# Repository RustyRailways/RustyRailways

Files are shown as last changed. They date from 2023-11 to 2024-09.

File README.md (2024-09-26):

# Rusty Railways

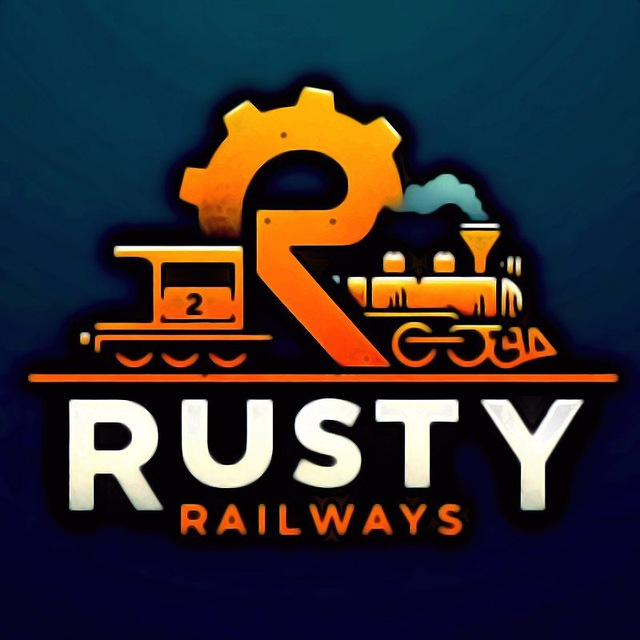
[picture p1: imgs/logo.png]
Rusty Railways Logo


## Description

Group Project by [**lucaSartore** (Sartore Luca)](https://github.com/lucaSartore), [**cattai-lorenzo** (Cattai Lorenzo)](https://github.com/cattai-lorenzo), [**MrLakige** (Callegari Michele)](https://github.com/MrLakige), [**Technorico** (Peruzzo Federico)](https://github.com/Technorico)
for [Embedded Software for The Internet of Things - 145996](https://unitn.coursecatalogue.cineca.it/insegnamenti/2023/95013/2019/10002/10712?annoOrdinamento=2019) taught by professor [Kasim Sinan Yildirim](https://webapps.unitn.it/du/it/Persona/PER0212812/Didattica) at [University of Trento, DISI Department](https://www.disi.unitn.it/).

This is a system that automates the motion of Lego trains and rail switches.
You can tell the system in which station you want a train to go (either using an HTTP request or using our GUI),
and the system will figure out the best way to achieve the goal, even moving trains that are on your
way if necessary. 

## Video

Watch the video (https://youtu.be/J4SjKY6N7vM)

## Components

The system is implemented using 5 different components:

 - `The Master`: This is the component that does all the calculations to find the optimal path, and then controls the trains and the switches, you can learn more about the master [here](./master/readme.md)
 - `The Client`: ([Godot](https://godotengine.org/) based client to create the train track and control/monitor the train system), you can learn more about the client [here](./client/README.md)
 - `The Map`: The map is a support data structure (a modified graph in particular) used by the master, you can learn more about the master [here](./map/readme.md)
 - `The Common Infrastructure`: The common infrastructure defines some basic messages that all components need to communicate with each other, as well as the IPs and the hardware abstraction layer traits, you can learn more about the master [here](./common_infrastructure/readme.md)
 - `The Trains`: You can learn more about the code that manages the trains [here](./train/rust/readme.md)
 - `The Switches`: You can learn more about the code that manages the switches [here](./switch/readme.md)

## Documentation

- [Common infrastructure documentation](https://rustyrailways.github.io/RustyRailways/common_infrastructure/doc/common_infrastructure/index.html)
- [Map documentation](https://rustyrailways.github.io/RustyRailways/map/doc/map/index.html)
- [Master documentation](https://rustyrailways.github.io/RustyRailways/master/doc/master/index.html)
- [Railway sim map documentation](https://rustyrailways.github.io/RustyRailways/railway_sim_map/doc/railway_sim_map/index.html)<br>
- [Switch documentation](https://rustyrailways.github.io/RustyRailways/switch/html/index.html)<br>
- [Train documentation](https://rustyrailways.github.io/RustyRailways/train/doc/locomotive/index.html)<br>

## Installation

Here you can find a quick list of the things you need to do, to try our project yourself.

### Master Installation
The current implementation of the master runs on a Linux system (e.g. Raspberry Pi with Raspberry Pi OS) so to run it, you just need to install the [regular rust toolchain](https://www.rust-lang.org/tools/install).
Given that we used a Hardware Abstraction Layer (HAL) to implement the master, with a bit more work, it can be executed on something smaller (like an ESP-32), if you are interested in this you can check out the train toolchain installation down below. 

### Train Toolchain Installation
The train code is written in embedded rust, with the [embedded-hal](https://github.com/rust-embedded/embedded-hal) and [embedded-svc](https://github.com/esp-rs/embedded-svc/tree/master) crates. To install the software needed to build for our target (The ESP-32) you can follow the tutorial [here](https://github.com/esp-rs/esp-idf-template?tab=readme-ov-file#prerequisites).

### Switch Toolchain Installation
To compile the switch code you can follow [this](./switch/readme.md) tutorial we have written.

### Client Installation
See [Client README.md](https://github.com/MrLakige/rusty_railways/blob/main/client/README.md).

### 3D Printing
Files to print the switch mechanism are located [here](./switch/hardware/Switch_3D_print/)
You can find a 3D printing tutorial [here](https://all3dp.com/1/cura-tutorial-software-slicer-cura-3d/).  

### Electronic Components

To build the switch PCB you can follow [this](switch#pcb) tutorial we have written

### Special Thanks

[FabLab UniTn](https://fablab.unitn.it/) for the space, tools and part of the materials used

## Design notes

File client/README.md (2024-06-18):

# Rusty Railways Client

This is a [Godot](https://godotengine.org/) based client to create the train track and control/see the status of the train system.

> [!WARNING]  
> This part of the project is currently broken, the code was fixed before the project presentation but never committed here properly with meaningful commits and comments in the code, I will try to do that whenever I find enough free time and willpower. Meanwhile you can use the [v0.1 release build](https://github.com/RustyRailways/RustyRailways/releases/tag/V0.1), it's an older version but it mostly works.

It lets you **Create** and **Edit** the **Train Track**, place the **NFC Tags**, **Trains** and **upload** (currently broken) everything to the Controller,
**Control** and **Monitor** the **Trains** and **Switches**.

### Screenshots
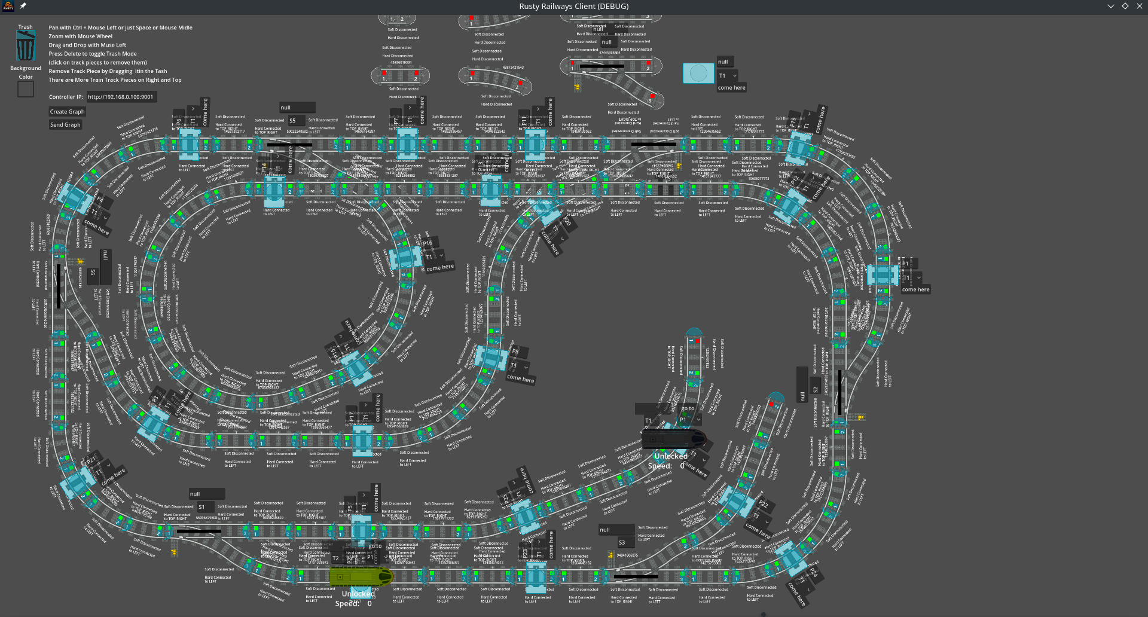
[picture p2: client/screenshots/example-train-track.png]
example-train-track


https://github.com/MrLakige/rusty_railways/assets/116217951/06c1ccc1-122a-48b4-8d96-e06f8fb9ee58

https://github.com/MrLakige/rusty_railways/assets/116217951/4c1d8071-14fc-486d-a815-6086c24b4450

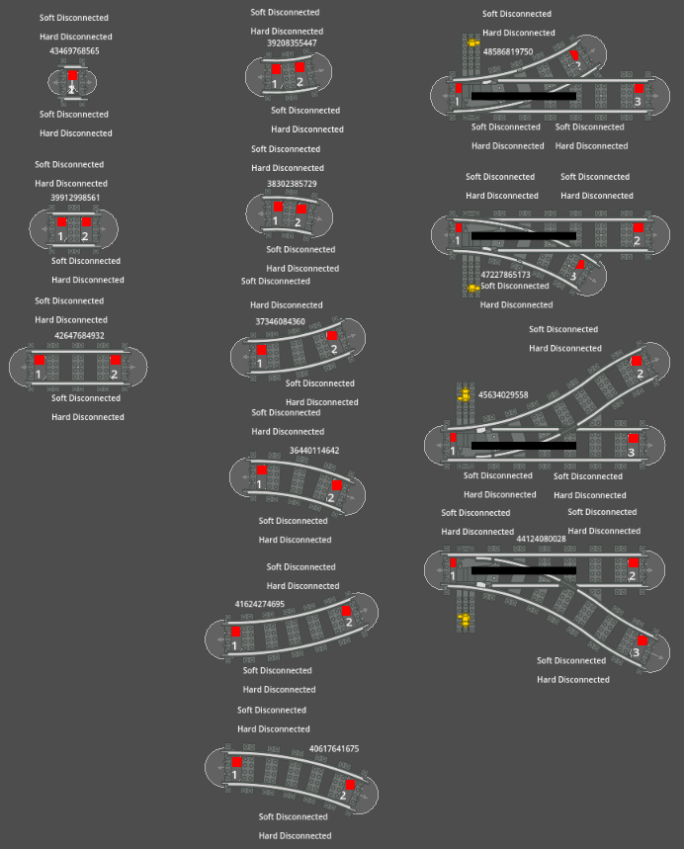
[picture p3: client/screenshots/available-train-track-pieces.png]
available-train-track-pieces


### Main Components
- Main (UI) ([Main.gd](./Main.gd) and [Main.tscn](./Main.tscn))
  - Create and Edit the Train Track, set IDs and Master IP

- HTTPIO ([HTTPIO.gd](./HTTPIO.gd))
  - Send move requests to Master (using HTTP with [this standard](./../master/src/high_level_controller#requests))

- Updaters ([TrainUpdatePosition.gd](./trains/TrainUpdatePosition.gd), [TrainUpdateStatus.gd](./trains/TrainUpdateStatus.gd), [TrainUpdateSpeed.gd](./trains/TrainUpdateSpeed.gd), [SwitchStateUpdater.gd](./trains/SwitchStateUpdater.gd))
  - Pools Train Positions, States, Speeds and Switch States data from Master (using HTTP with [this standard](./../master/src/high_level_controller#requests))

### Installation (from pre-made builds)
Download the latest master build for your OS from the [latest release page](https://github.com/MrLakige/rusty_railways/releases/latest) under `Assets` and launch it, the following builds are currently available:

- Linux x86_64
- Windows x86_64
- MacOS x86_64

https://github.com/MrLakige/rusty_railways/releases/download/V0.1/linux-x86_64-rusty-railways-client.x86_64

If you need a build for a different system and/or architecture please follow the [Installation (from source)](#Installation (from source)) section.

### Installation (from source)
Install the latest Godot 4 Version ([Steam App](https://store.steampowered.com/app/404790/Godot_Engine/), [Standalone Installer](https://godotengine.org/download/windows/), [Flatpak (Linux only)](https://flathub.org/apps/org.godotengine.Godot) or [WinGet (Windows only)](https://winstall.app/apps/GodotEngine.GodotEngine))

Clone the repository with 
```bash
git clone https://github.com/MrLakige/rusty_railways.git
```

Open 
```bash
./rusty_railways/client/project.godot
```

Go to `Project` -> `Export...` and choose one of the pre-made `Presets` or use `Add...` to add a new custom preset with a different system and/or architecture of your choice.

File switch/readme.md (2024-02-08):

# ESP-8266 Rail Track Switch Control System

This section of the repository contains the source code for an ESP-8266-based rail track switch control system. The code enables the `ESP-8266` to function as a web server, offering control over a servo-driven rail track switch. It is designed to set the correct path for trains.

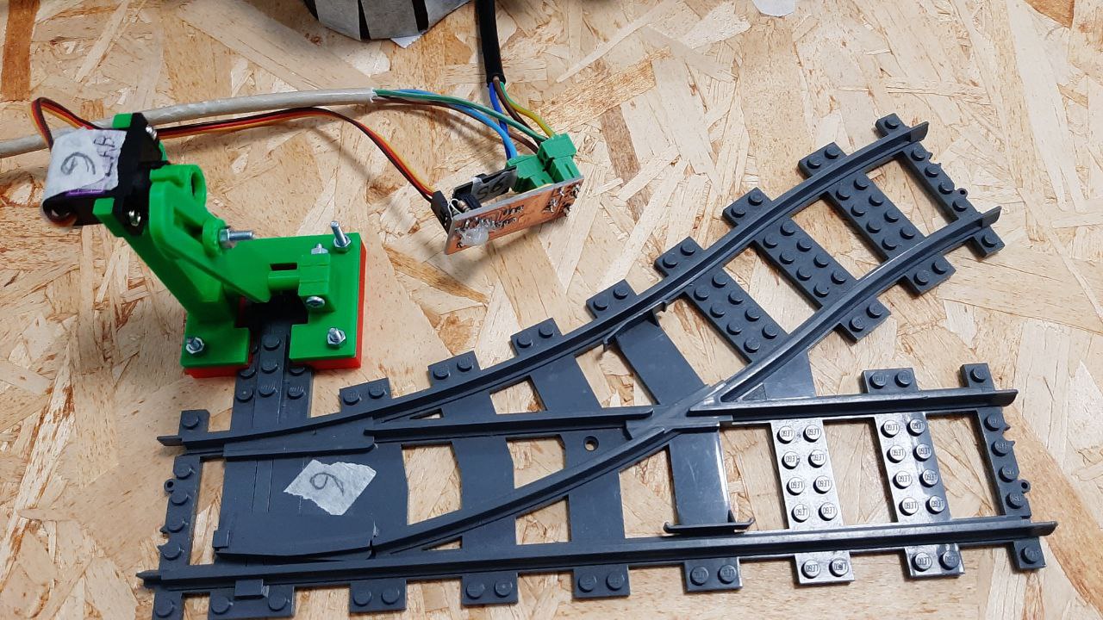
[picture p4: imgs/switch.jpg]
Switch Image


## Features
- The `ESP-8266` uses a REST API to interface with the other components of the project.
- Switch control commands can be transmitted via HTTP POST requests.

## Hardware
- The system utilizes a Servo motor (specifically, the `MSG90S`) to control the position of the rail track switch.
- WiFi connectivity is established using the built-in wireless functionality of the `ESP-8266` module.

## Code Overview
- The code includes essential libraries such as `ESP8266WiFi`, `WiFiClient`, `ESP8266WebServer`, `Arduino`, `Servo`, and `ArduinoJson`.
- Switch positions are defined based on user-configurable constants.
- The web server responds to HTTP GET requests with information about the switch and handles HTTP POST requests to control the switch position.

## Requirements
- [PlatformIO](https://platformio.org/platformio-ide) (Follow the [guide to download and configure](https://docs.platformio.org/en/latest/core/installation/index.html))
- PlatformIO compiler toolchain (Download [here](https://registry.platformio.org/platforms/platformio/espressif8266/installation))

## Configuration
1. Modify the WiFi credentials by adjusting the `STASSID` and `STAPSK` constants.
2. Specify the switch characteristics by defining the switch name and position angles for the servo in the code.
   (In our demo it is possible to select one of the predefined configurations of the six switches present on the map, using a compiler directive modifiable in the [platformio.ini](./platformio.ini))

## Usage
1. Connect the `ESP-8266` to the rail track switch control mechanism.
2. Flash the firmware using this command:  
   ```bash
      platformio run --target upload`
   ```
### Troubleshooting
#### If a library is not found
1. Run:  
    ```bash
    pio lib install
    pio update
    ```
#### If PlatformIO is not found
1. Ensure that PlatformIO and the toolchain are installed correctly.
2. Verify that the PlatformIO global variable is set.  
   Command:
   ```bash
      source /your_local_path_to/ENV/bin/activate
   ```
## Supported Hardware Parts:
>[!CAUTION]
>⚠️ **BASIC CNC AND ELECTRONICS KNOWLEDGE IS NEEDED TO REPRODUCE BELOW STEPS** ⚠️
### PCB
Files to create the PCBs are located [here](./hardware/Switch_PCB).
#### To Design and Mill a PCB:
You will require the following software:
- [KiCad](https://www.kicad.org/)
- [FlatCAM](http://flatcam.org/)
- GRBL Controller, like [Candle](https://github.com/Denvi/Candle)

#### To mill the PCB of the Switch:
>[!IMPORTANT]
>GRBL Controller or a GCode for CNC/NC controller for your CNC is required.
1. Download the .nc files from [here](./hardware/Switch_PCB/FlatCAM/OutputFiles)
2. Load in the _CNC Program_ / _NC Code Feeder_ the [file](./hardware/Switch_PCB/FlatCAM/OutputFiles/Switch_PCB_ESP01-F_Cu.gbr_cnc_file.nc) with _F_Cu_ in his name, to make the isolation of the traces of the PCB circuit.
3. Then load in this sequence, the following files: [0.8mm](./hardware/Switch_PCB/FlatCAM/OutputFiles/Switch_PCB_ESP01-PTH_0.8mm.drl_cnc.nc), [1.0mm](./hardware/Switch_PCB/FlatCAM/OutputFiles/Switch_PCB_ESP01-PTH_1.0mm.drl_cnc.nc), [Edge_Cuts](./hardware/Switch_PCB/FlatCAM/OutputFiles/Switch_PCB_ESP01-Edge_Cuts.gbr_cutout_cnc.nc).

___
### Images for reference

<p float="left">
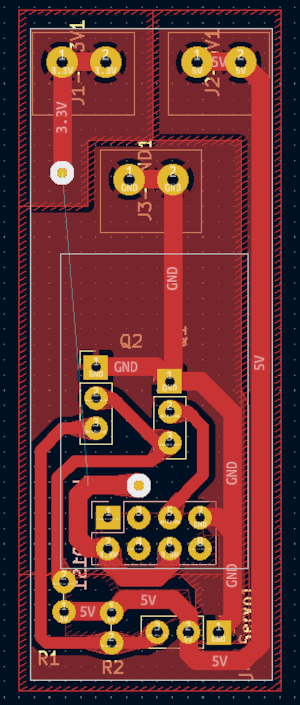
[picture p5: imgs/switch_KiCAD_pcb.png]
   
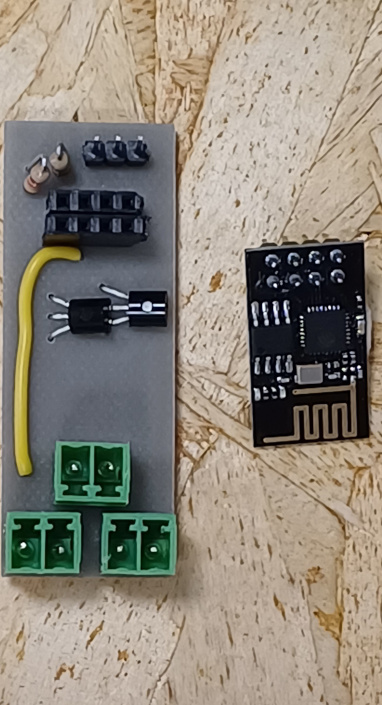
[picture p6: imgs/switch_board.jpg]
   
</p>

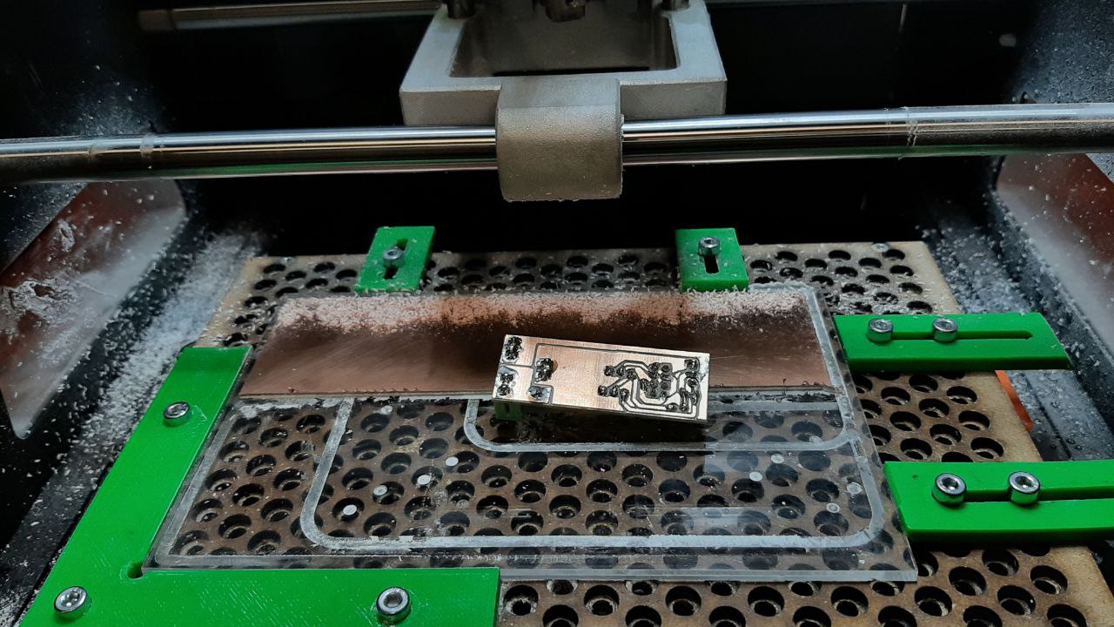
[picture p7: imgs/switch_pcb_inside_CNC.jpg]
Switch PCB inside CNC


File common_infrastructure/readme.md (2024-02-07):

# Common infrastructure

This crate defines some common components that are in use in all the other creates, in particular:

 - `Position` is an enum that represents all of the possible positions the train can be on, in reality, the position is identified by an RFID tag that can be read from an NFC reader, so the enum can be created from an array of 4 bytes.

 - `Train` is an enum that represents all the trains
 - `Switch` is an enum that represents all the switches in the map
- `urls` is a module that defines all the IPs and URLs of the components involved in the system
- `hals` is a module that defines some traits for the components involved in the system, these traits are used to abstract the hardware, to make it possible to run the same code on different hardware configurations. There are 3 main _HAL_s defined:
  - `GenericHal` is the _HAL_ that defines the basic functionalities, and all of the other HALs inherit from this.
  - `MasterHal` is the _HAL_ for the master/brain of the operation
  - `TrainHal` is the _HAL_ for the train
  - `HeartBeatManagerHal` is a _HAL_ for an optional component that can be used for additional safety that allows the system to detect if a component is disconnected. This is not in use in the current implementation of the master and the train
  
Note: the switch does not have a _HAL_ because our switches run on `ESP-8266` that are not supported in embedded rust.

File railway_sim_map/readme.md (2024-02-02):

# Railway sim map

This create contains a simulated version of the real world map, this is done by implementing the master's HAL and executing all the actions in a virtual world.

This has been used to develop the master quicker without having to debug on real world components

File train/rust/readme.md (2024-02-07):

# Locomotive Part

## Description

This section of the repository focuses on the train component of the project. Each train is equipped with an `ESP-WROOM-32` for motor control and communication via WiFi, along with an NFC RFID reader. The code is written in Rust, based on the Rust Embedded HAL framework. The benefits of using Rust Embedded include a common infrastructure used among all projects, better code reusability, and better memory safety.

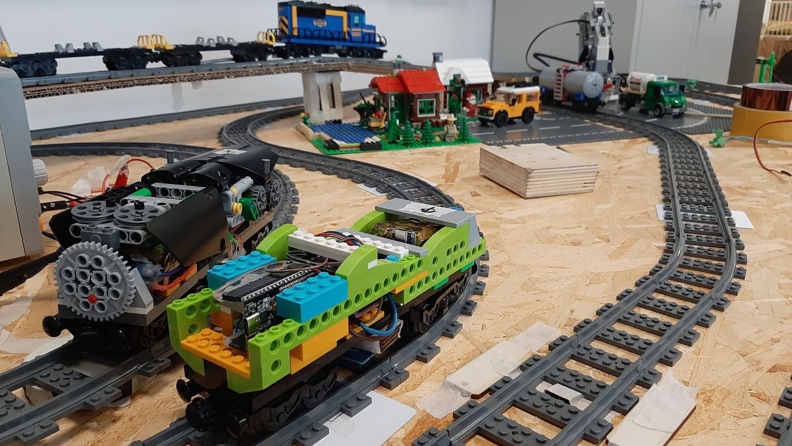
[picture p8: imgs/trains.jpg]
Trains Image


## Hardware schematics

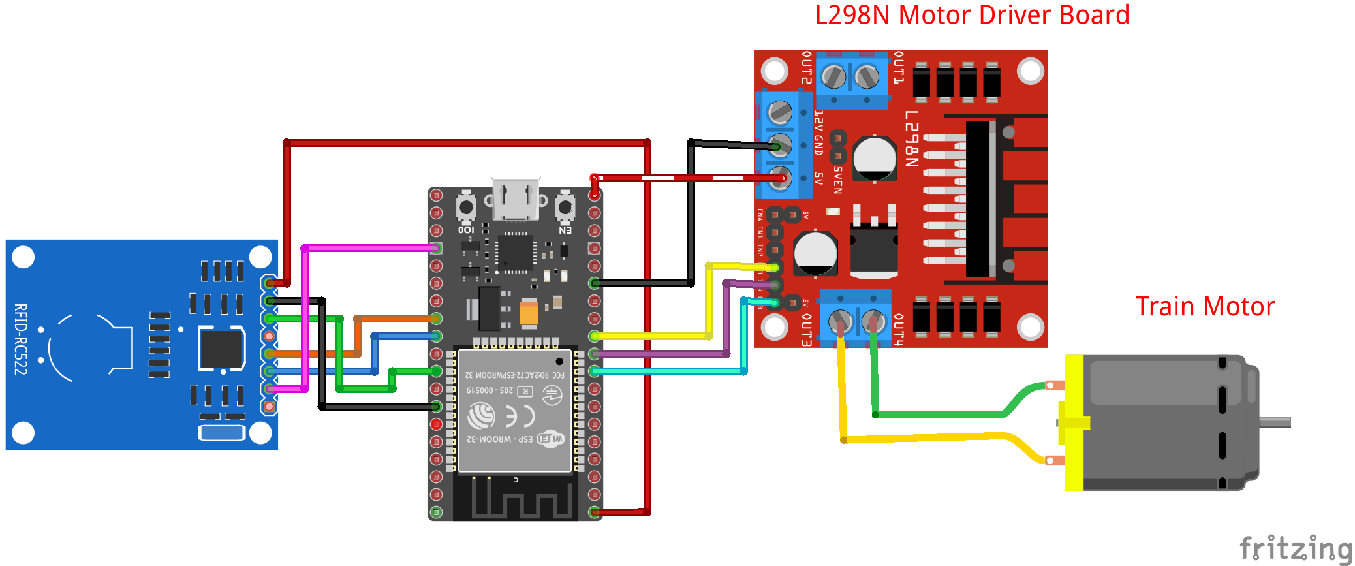
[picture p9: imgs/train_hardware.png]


 - Motor control pins:
    - pwm_pin      -> `GPIO25`
    - forward_pin  -> `GPIO26`
    - backward_pin -> `GPIO27`
 - NFC reader pins:
    - SCK          -> `GPIO15`
    - MISO         -> `GPIO16`
    - MOSI         -> `GPIO17`
    - SS/Reset     -> `GPIO18`

## Features

The features include reading NFC tags placed on the track, WiFi communication, and motor control. Each feature is implemented in specific files according to the Rust HAL framework.

## Hardware

Trains locomotives are composed of an `ESP-WROOM-32`, `H-bridge L298N`, `NFC/RFID reader MFRC-522`, and a `Li-Ion custom battery pack`.

## Requirements

Before proceeding, ensure that the main requirements are installed. Refer to the [main project guide](../../README.md) for details. Follow [this guide](https://github.com/esp-rs/esp-idf-template/tree/master#prerequisites) to download and install all the necessary files and toolchains required to run this part of the project.

### If Some Libraries Are Missing:

1. Run the following command to install the required dependencies:
    ```bash
    sudo apt-get install git wget flex bison gperf python3 python3-pip python3-venv cmake ninja-build ccache libffi-dev libssl-dev dfu-util libusb-1.0-0
    ```

2. If facing issues installing **libuv-dev**, follow this [solution](https://stackoverflow.com/questions/32438367/install-libuv-on-ubuntu-12-04):
    ```bash
    sudo apt-get install libudev-sys
    sudo apt-get install libudev-dev 
    ```

## Compile and Execution

1. Initialize:
   ```bash
   make init
   ```
3. Compile:
   ```bash
   make build
   ```
5. Connect the ESP32 and flash:
   ```bash
   make flash
   ```
7. (Optional) For debugging, check the serial output:
   ```bash
   make monitor
   ```

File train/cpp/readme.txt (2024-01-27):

command:
source ./ENV/bin/activate
platformio init --board esp12e

git clone https://github.com/Links2004/arduinoWebSockets.git

platformio run --target upload
pio device monitor

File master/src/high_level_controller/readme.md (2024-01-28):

# High level controller

The high level controller is the component that communicate with the GUI and control the
path finder and scheduler.

## Requests

The high level controller spawn a web server that can receive requests from the GUI.  
All the requests will be done at at the ip `IP_MASTER` and port `MASTER_PORT_VISUALIZER` (see the [common infrastructure](../../../common_infrastructure/src/urls.rs)).

The handler supported are:

 - `POST /add_request`: add a new request to the scheduler  
   examples:
    - `{"MoveTrain": ["T1","P3"]}`
    - `{"LockTrain": ["T1"]}`
    - `{"UnlockTrain": ["T1"]}`
 - `GET /train_position/{id}` return the position of the train  
   example: 
   - `"P1"`
 - `GET /train_status/{id}` return the status of the train,  
    examples: 
   - `"Locked"`
   - `"Unlocked"`
   - `"Moving"`
 - `GET /train_speed/{id}` return the speed of the train, as a signed 8-bit integer  
    example: 
   - `10`
 - `GET /switch_position/{id}` return the position of the switch  
    examples: 
   - `"Straight"`
   - `"Diverted"`

Note 1: `id` is an integer, and is the id of the train or switch.
for example `id=1` is equal to the train `T1` or the switch `S1`.

Note 2: All the get methods can return null if the train or switch is not found. 

## Response
 All the response are in TEXT format, if an error occurs the code will be `500` and the body will be the error message.

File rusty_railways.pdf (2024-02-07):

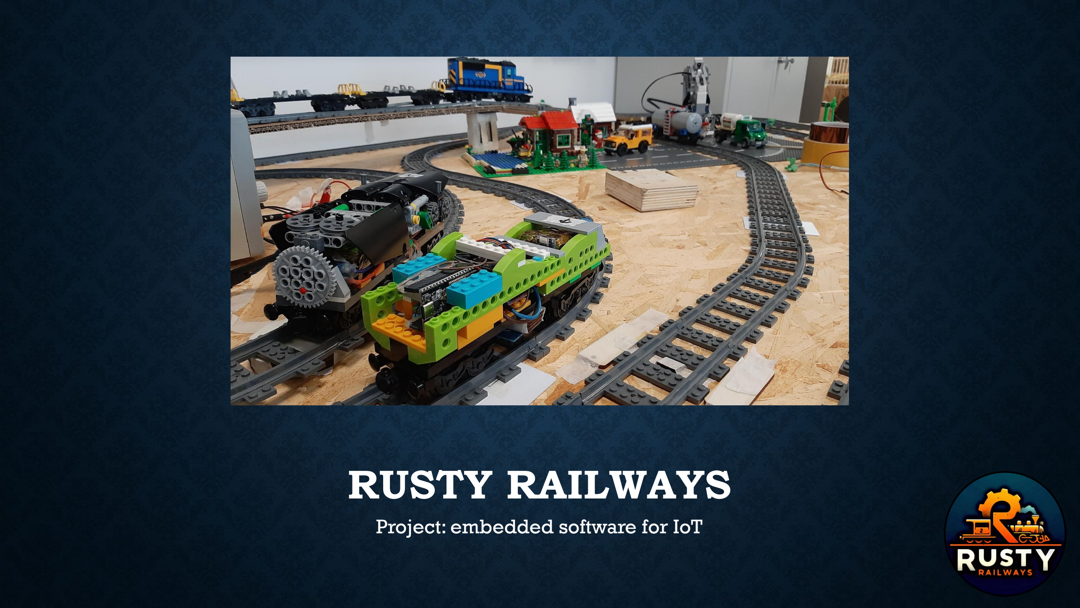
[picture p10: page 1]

# RUSTY RAILWAYS

## Project: embedded software for IoT

# MASTER

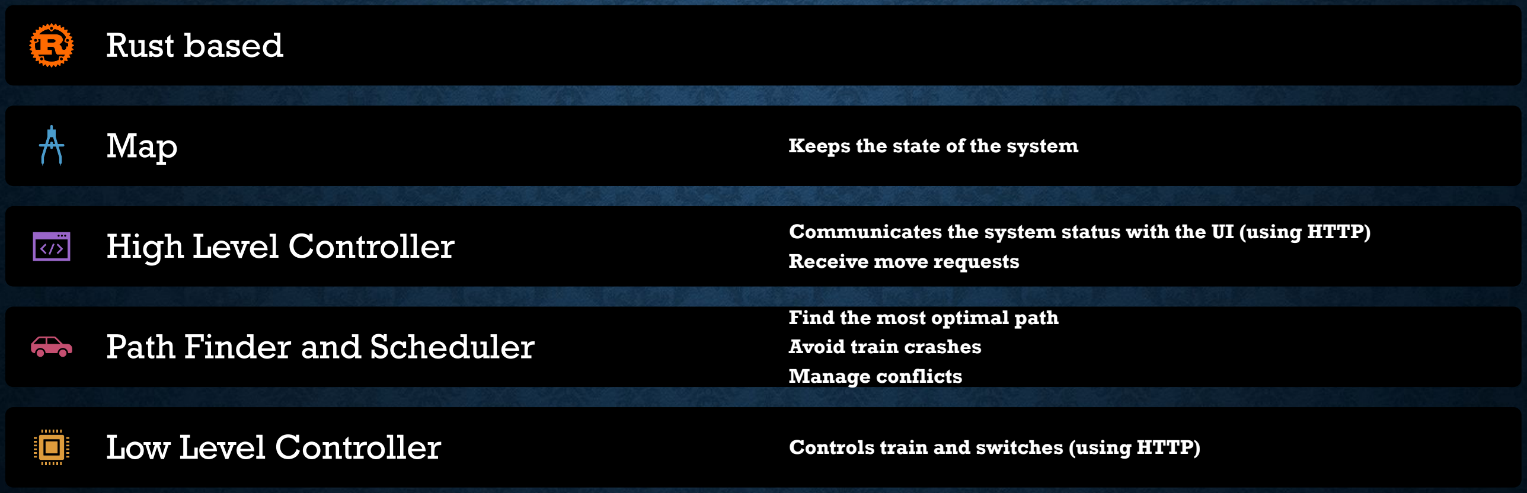
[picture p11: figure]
Rust based; Map; Keeps the state of the system; Receive move requests; Path Finder and Scheduler; Find the most optimal path; Avoid train crashes; Manage conflicts

High Level Controller | Communicates the system status with the UI (using HTTP)
Low Level Controller | Controls train and switches (using HTTP)

# TRAIN

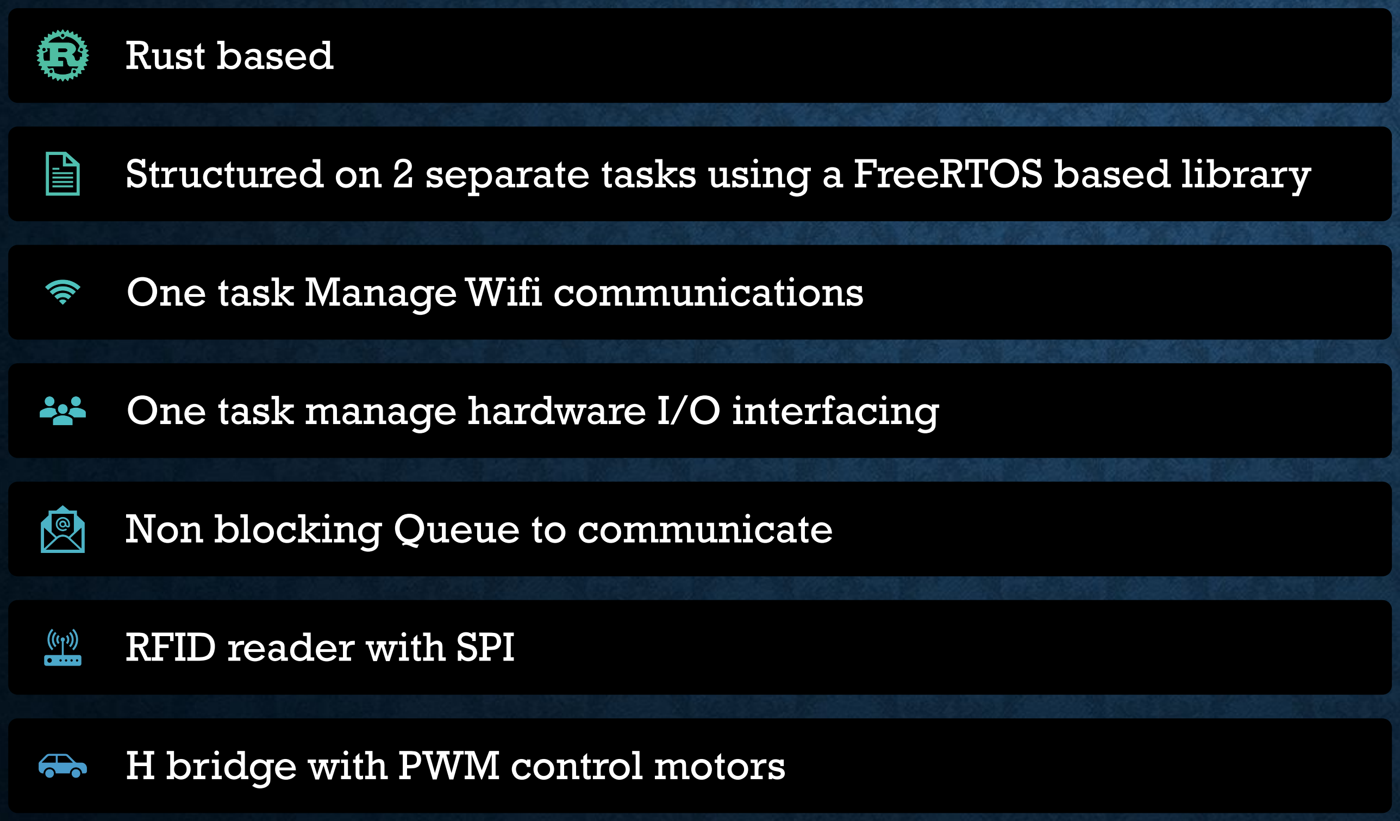
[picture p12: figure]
Rust based; One task Manage Wifi communications; Non blocking Queue to communicate; RFID reader with SPI; H bridge with PWM control motors
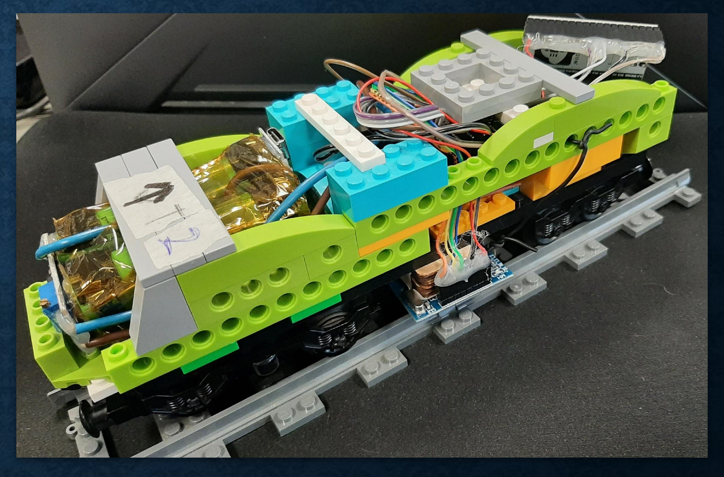
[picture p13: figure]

Structured on 2 separate tasks using a FreeRTOS based library

One task manage hardware I/O interfacing

# RAILWAY SWITCHES

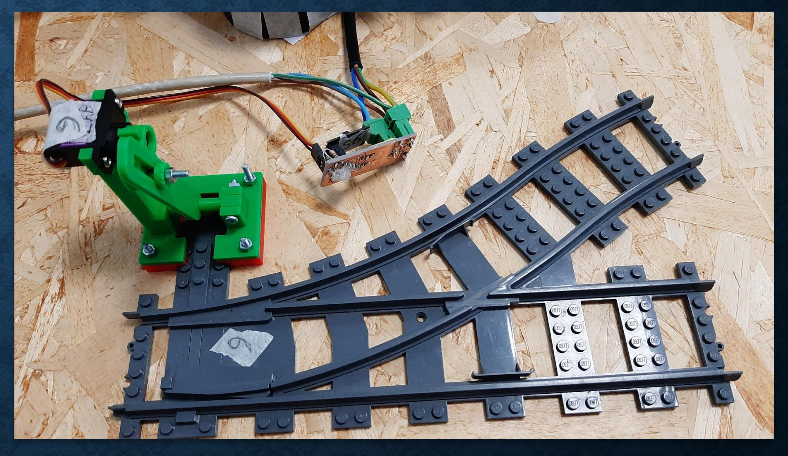
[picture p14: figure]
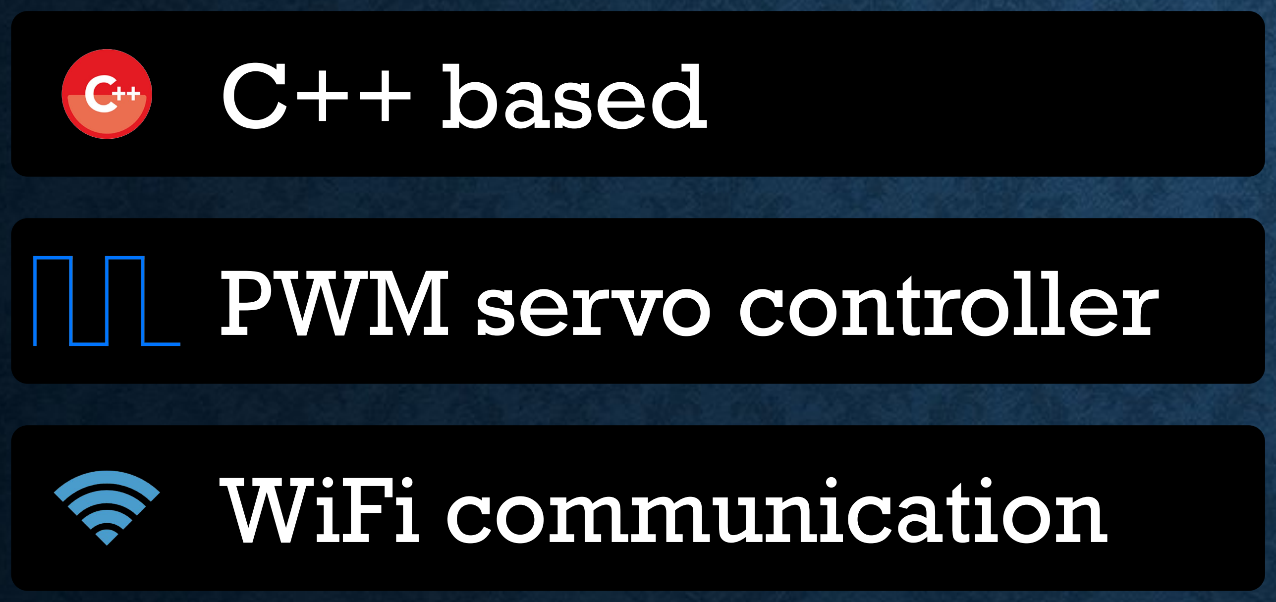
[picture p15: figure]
C++ based; PWM servo controller; WiFi communication

# CLIENT (GUI)

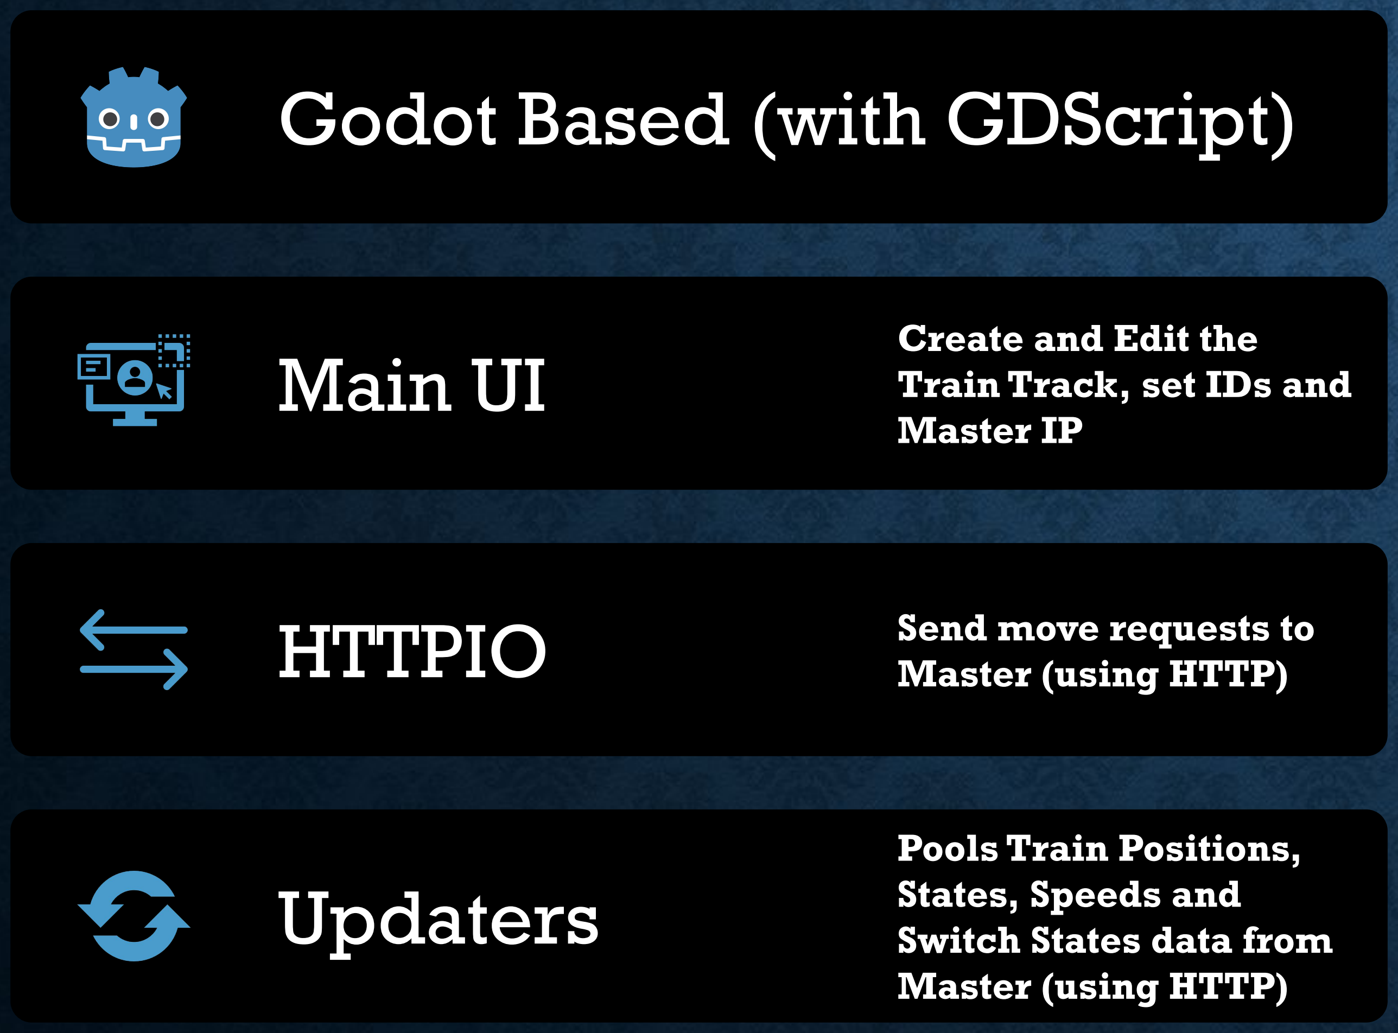
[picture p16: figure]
Godot Based (with GDScript); Main UI; Create and Edit the Train Track, set IDs and Master IP; HTTPIO; Send move requests to; Master (using HTTP); Updaters; Pools Train Positions, States, Speeds and Switch States data from Master (using HTTP)
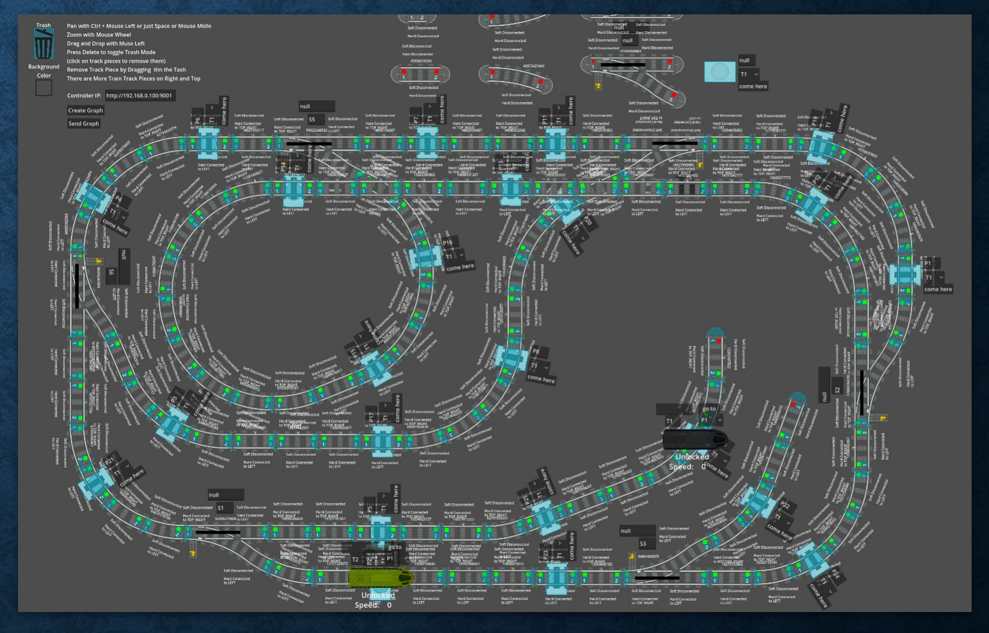
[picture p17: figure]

# STRUCTURE AND TESTING

## - All Rust components are split into hardware

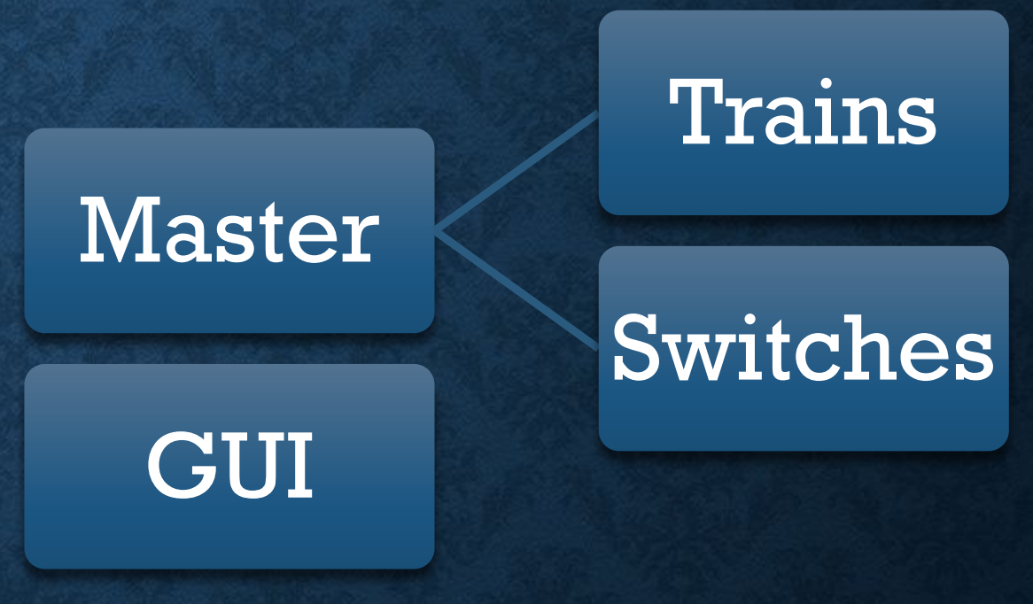
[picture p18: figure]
Master; Trains; Switches; GUI

## dependent and hardware independent parts

using rust’s Trait System Example (https://mrlakige.github.io/rusty_railways/common_infrastructure/doc/common_infrastructure/hals/trait.TrainHal.html)

## - The entire system has been recreated in a

simulation (https://github.com/MrLakige/rusty_railways/tree/main/railway_sim_map) to test all the master’s feature

## without the needs of a physical system

- The master has also 30+ automated unit | test (https://github.com/MrLakige/rusty_railways/blob/main/map/src/map_tests.rs#L115)
- All the code is fully covered by | documentation (https://mrlakige.github.io/rusty_railways/)

## tanks to doxygen and rustdoc

# FUTURE IMPLEMENTATIONS

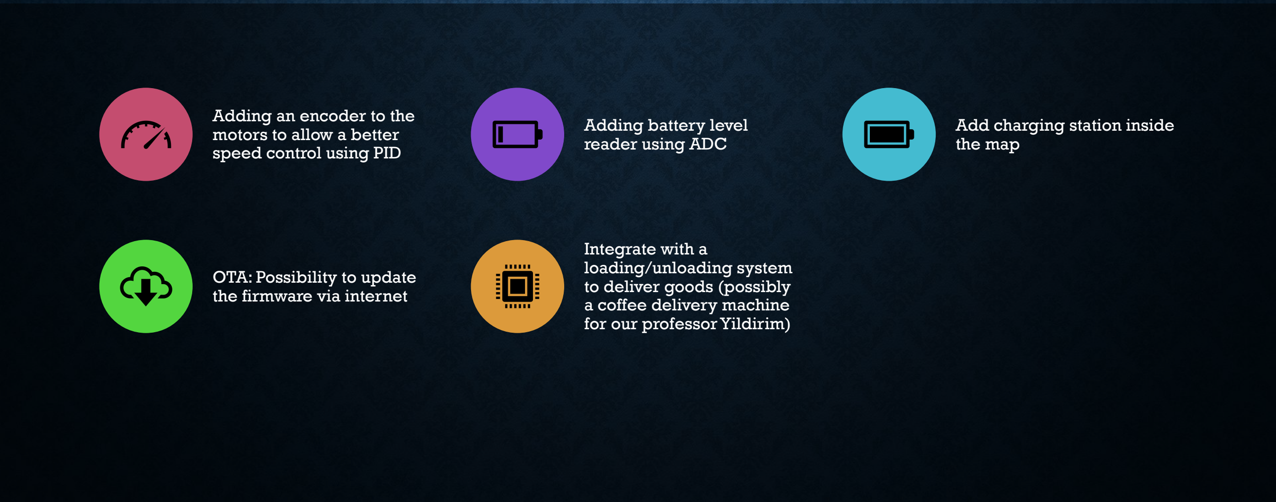
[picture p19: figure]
Adding an encoder to the motors to allow a better speed control using PID; Adding battery level reader using ADC; Add charging station inside the map; OTA: Possibility to update the firmware via internet; Integrate with a loading/unloading system to deliver goods (possibly a coffee delivery machine for our professor Yildirim)

# CONTRIBUTIONS

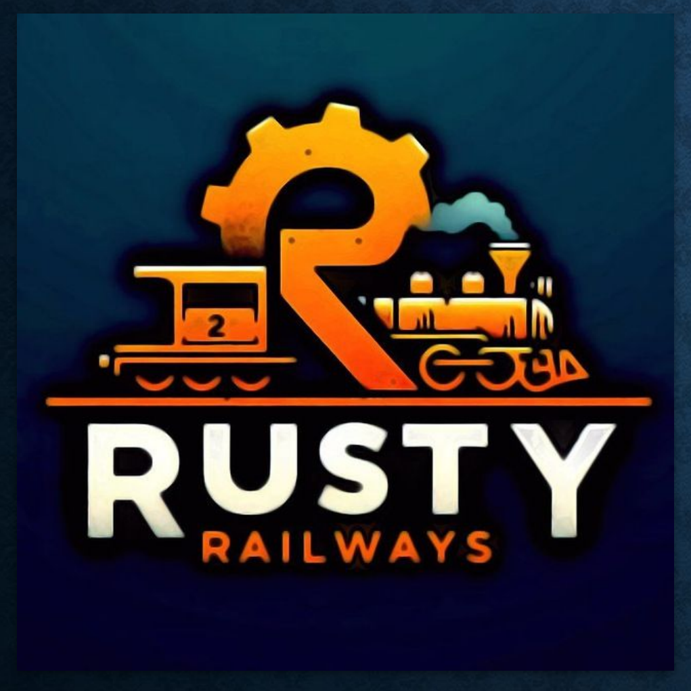
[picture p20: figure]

Master:

- Low Level Controller: Federico Peruzzo
- Path Finder And scheduler: Luca Sartore
- High Level Controller: Lorenzo Cattai

Trains: Luca Sartore and Michele Callegari

Switches: Michele Callegari

Graphical user interface: Lorenzo Cattai

Electronic Design, testing and manufacturing: Federico Peruzzo

3D Design: Luca Sartore

Git Repository: https://github.com/MrLakige/rusty_railways

A Special tanks to the UniTn FabLab Team!

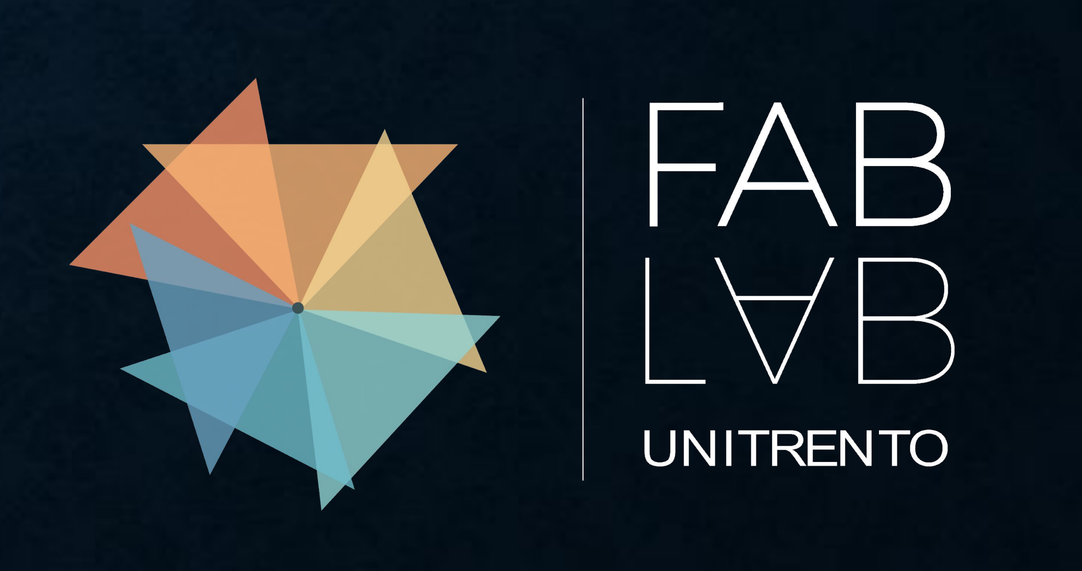
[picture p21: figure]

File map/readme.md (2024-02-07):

# Map

Basically, the map is a wrapper structure for a graph with some specific features that are used for our implementation.

In the graph, a node represents a position, (aka an NFC tag) in the real world.

The tags are used for:
 - Tel the train when to stop for a station
 - Track the position of the train and stop if it takes the wrong path
 - Regulate the train speed for tracks with different slope/curvature radius

A link in a map contains the length of the link and the maximum speed the train is allowed to reach on that track. The speed can be different depending on the direction the train is going (this is useful for example in a slope).

## Implementation

### The Initialized-Uninitialized States

The map is written using a generic-structure, where the generic parameters _S_ represent the states (that can be `Initialized` or `Uninitialized`).
Inside the graph, some `References` are used to point to `Nodes`, `Trains`, and `Switches`.
In the map, a reference is a structure that points to an object (e.g. a train has inside a reference to the station it is currently on).
The [references](references/mod.rs) can also have two states (`Initialized` or `Uninitialized`).  
To understand this distinction let's make an example with a reference to the position `P1`  

In the case of an Uninitialized map, a reference will just contain an enum
`Position::P1`. This is good for simplicity, as it avoids having to deal with pointers, it also allows us to make the map structure serializable and deserializable to JSON using `serde` and `serde/json`.
The only problem is that the performances are not as good compared with 
having a pointer/reference.

In the case of an Initialized map, the reference is replaced with a raw pointer, that allows for quick access to the item referenced.

#### The use of unsafe

We wanted to derive the serialize/deserialize trait, and this can only be done with the uninitialized state of the map, as we cannot deserialize a reference/pointer to a variable.  

Unfortunately as of today (02/2024), due to Rust characteristics and implementation, is impossible to decide to derive the serialize/deserialize (or any other Trait) only for a version with type _T_ of a generic structure (e.g. talking about our project we cannot derive _serialize_/_deserialize_ for Map\<_Uninitialized_> without also deriving it for Map\<_Initialized_>). To avoid this we have implemented manually the serialize/deserialize for the initialized reference, with just a panic that explains that the function should never be used.
Then we had to use raw pointers instead of references inside the initialized Map reference because using a lifetime would prevent us from implementing the deserialize trait.

## Map views

The map has many functionalities, to simplify the life of the user some `Views` have been created, in particular:
 - [Map creation view:](src/views/map_creation_view.rs) is a view used to quickly and easily build a map
 - [Map controller view:](src/views/map_controller_view.rs) is a view designed to control the map (e.g. move the train/the switches...)
 - [Map visualization view:](src/views/map_visualization_view.rs) is a view designed to give information about the map, like having the speed and status of trains
 - [Map navigation view:](src/views/map_visualization_view.rs) exposes some high-level APIs to navigate the map as a graph and find the best path
 - [Map factory:](src/views/map_factory.rs) is a factory that allow to create different views.

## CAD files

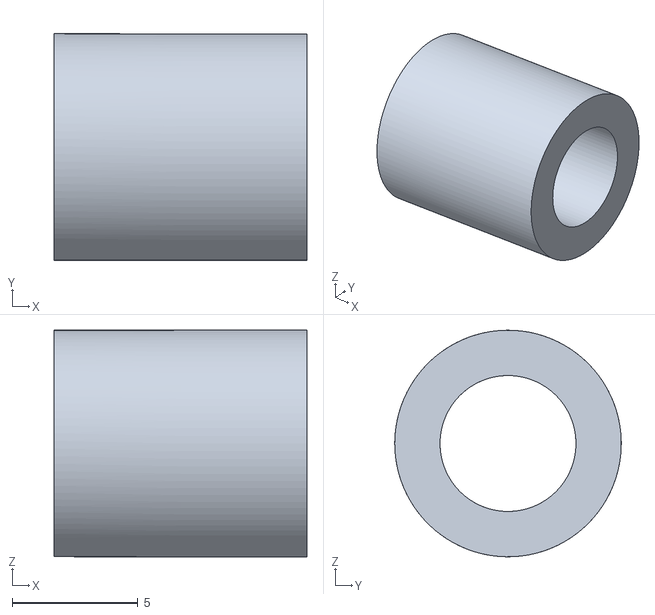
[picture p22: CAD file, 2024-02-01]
switch/hardware/Switch_3D_print/Spacer.stl
10.1 x 9.00 x 9.00

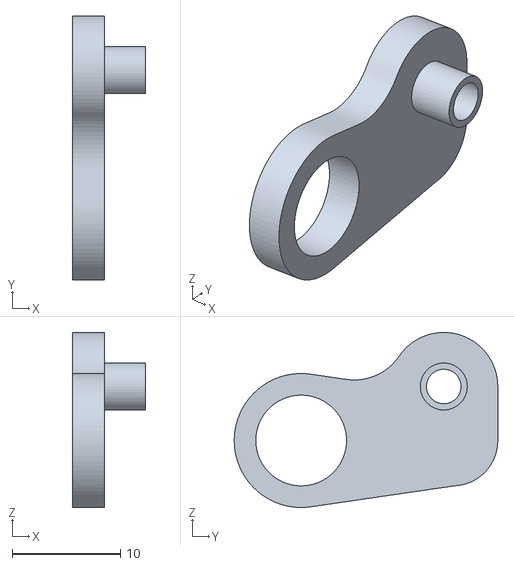
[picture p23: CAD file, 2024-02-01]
switch/hardware/Switch_3D_print/servo arm 2.stl
6.80 x 24.4 x 16.2

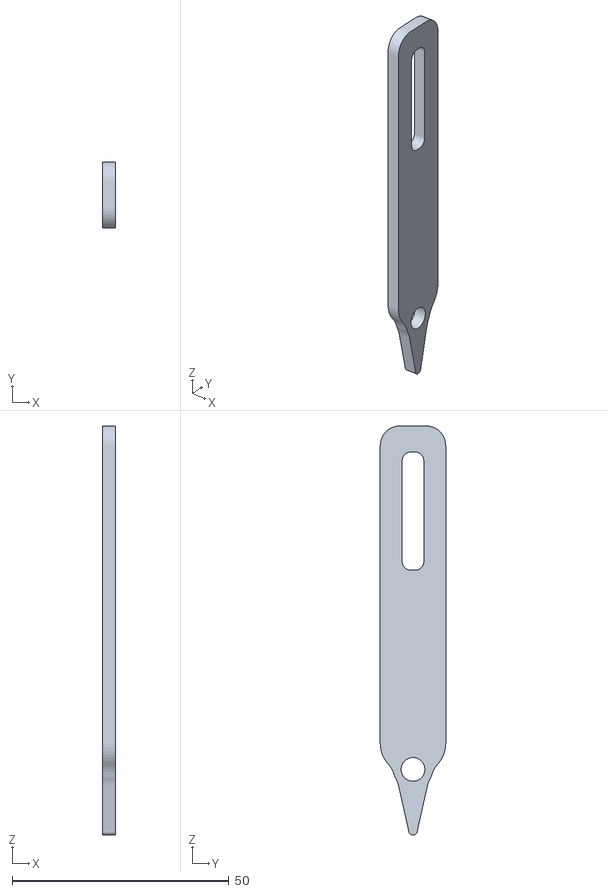
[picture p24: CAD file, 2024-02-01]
switch/hardware/Switch_3D_print/Perno.stl
3.10 x 15.1 x 94.4

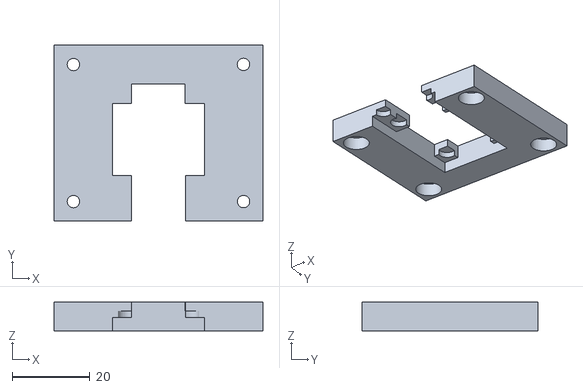
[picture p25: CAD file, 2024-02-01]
switch/hardware/Switch_3D_print/P1.stl
53.8 x 45.3 x 7.40

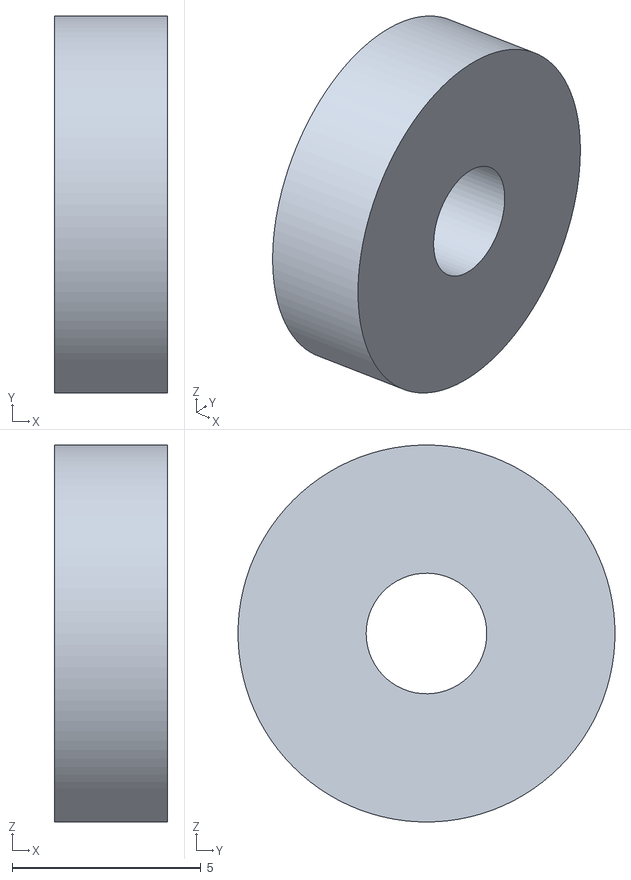
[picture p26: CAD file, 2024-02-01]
switch/hardware/Switch_3D_print/servo arm 3.stl
3.00 x 10.0 x 10.0

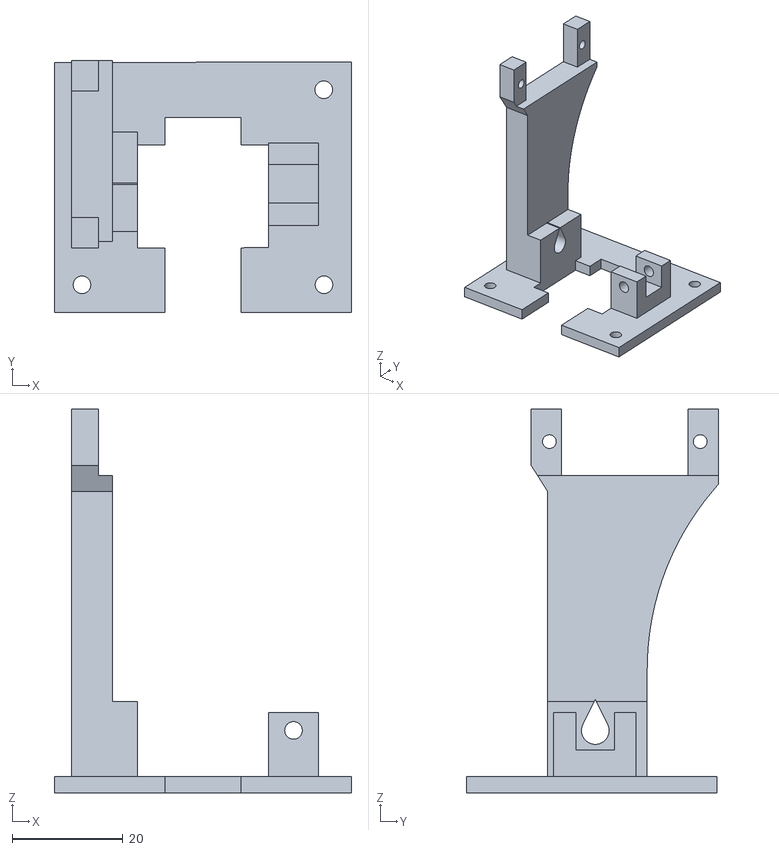
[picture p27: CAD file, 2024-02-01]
switch/hardware/Switch_3D_print/P2.stl
53.8 x 45.6 x 69.5

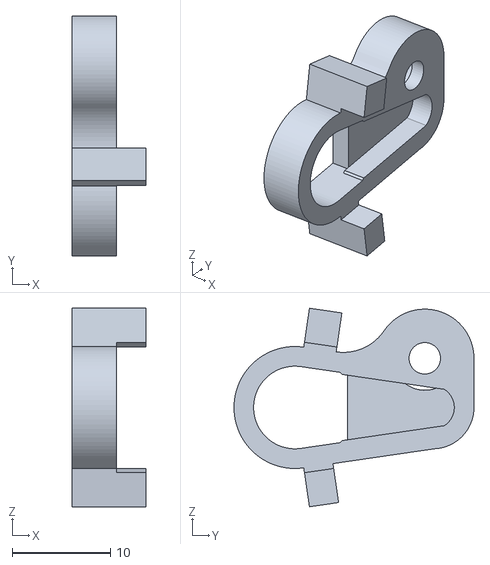
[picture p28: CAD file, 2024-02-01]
switch/hardware/Switch_3D_print/servo arm.stl
7.50 x 24.4 x 20.2

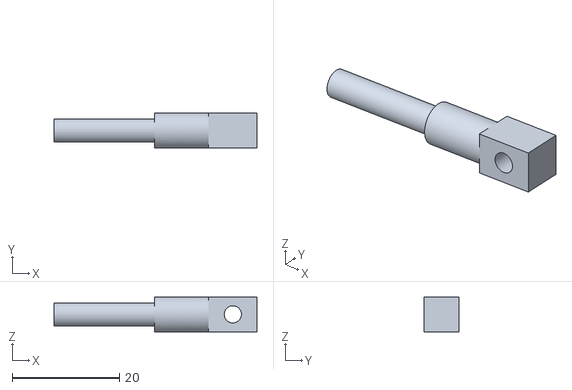
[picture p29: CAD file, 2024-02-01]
switch/hardware/Switch_3D_print/Asse.stl
37.8 x 6.50 x 6.50

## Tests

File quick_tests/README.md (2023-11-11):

# Quick Tests
This folder contains project that are useful to test the hardware quickly.

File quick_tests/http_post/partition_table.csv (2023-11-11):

# ESP-IDF Partition Table
# Name | Type | SubType | Offset | Size | Flags
nvs | data | nvs | 0x9000 | 0x6000
phy_init | data | phy | 0xf000 | 0x1000
factory | app | factory | 0x10000 | 3M

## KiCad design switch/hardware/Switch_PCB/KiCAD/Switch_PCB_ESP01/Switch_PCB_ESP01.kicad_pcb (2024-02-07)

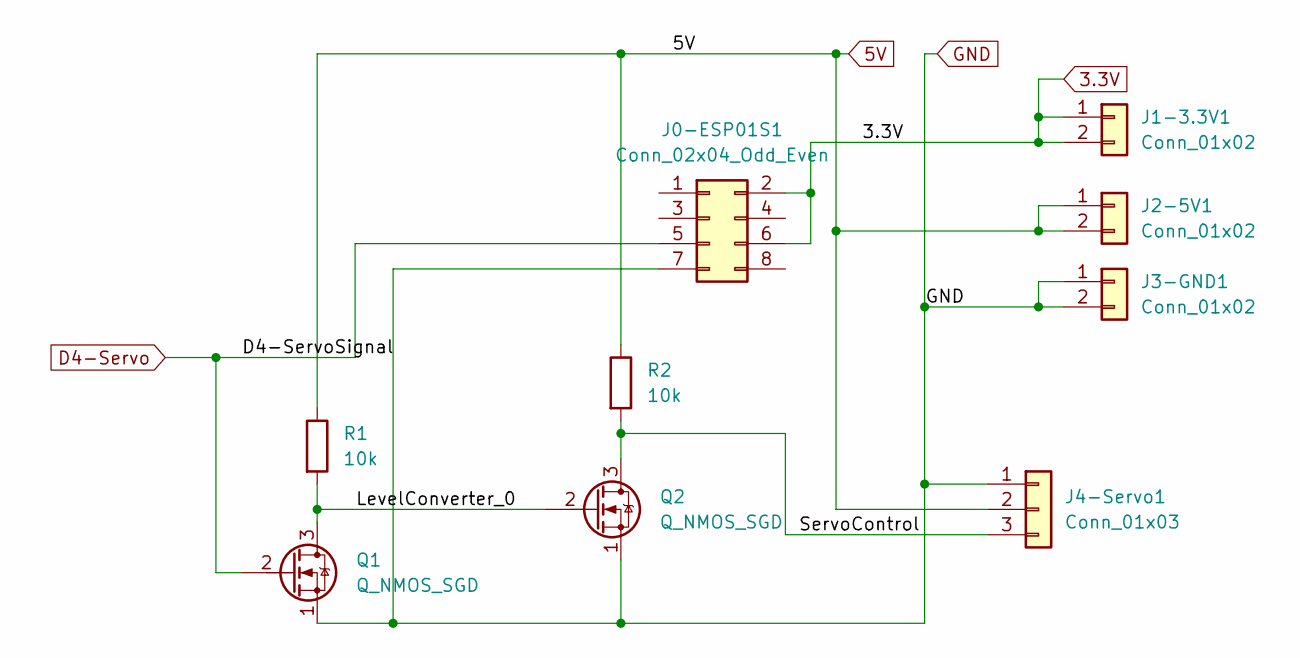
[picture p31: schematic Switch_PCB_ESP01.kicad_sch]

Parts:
J0-ESP01S1: Conn_02x04_Odd_Even; ESP01
J1-3.3V1, J2-5V1, J3-GND1: Conn_01x02; 01x02_TerminalBlock
J4-Servo1: Conn_01x03; PinHeader_1x03_P2.54mm_Vertical
Q1, Q2: Q_NMOS_SGD; PinHeader_1x03_P2.54mm_Vertical
R1, R2: 10k; R_Axial_DIN0204_L3.6mm_D1.6mm_P2.54mm_Vertical

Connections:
3.3V: J0-ESP01S1.2, J0-ESP01S1.6, J1-3.3V1.1, J1-3.3V1.2
5V: J2-5V1.1, J2-5V1.2, J4-Servo1.2, R1.1, R2.1
/LevelConverter_0: Q1.3 (D), Q2.2 (G), R1.2
/ServoControl: J4-Servo1.3, Q2.3 (D), R2.2
D4-Servo: J0-ESP01S1.5, Q1.2 (G)
GND: J0-ESP01S1.7, J3-GND1.1, J3-GND1.2, J4-Servo1.1, Q1.1 (S), Q2.1 (S)

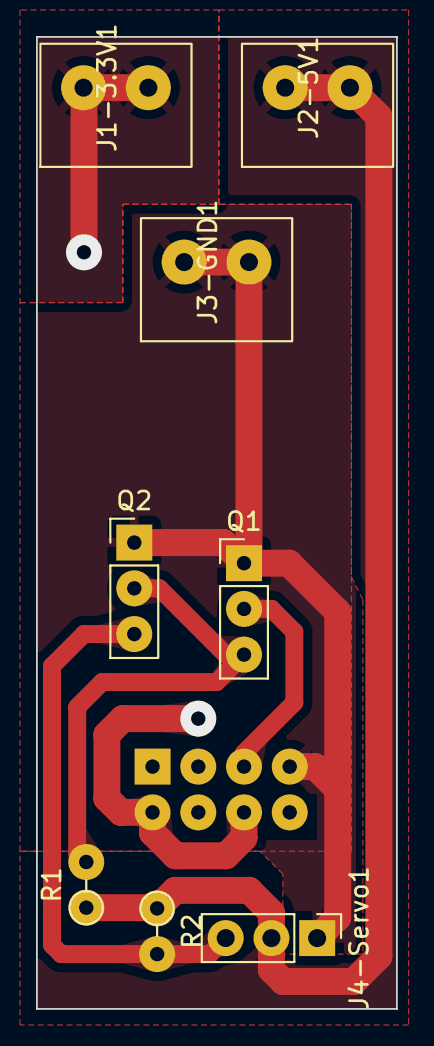
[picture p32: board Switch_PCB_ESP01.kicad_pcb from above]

Board: 2 copper layers, 20.0 x 54.0 mm, 9 parts (1 on the bottom side), 6 nets.

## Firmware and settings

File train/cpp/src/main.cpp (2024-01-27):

#include <Arduino.h>
#include <WebSocketsServer.h>
#include <ArduinoJson.h>
#include <WiFi.h>
#include <Adafruit_PN532.h>

// motor pin
#define MOTOR_PIN1 19
#define MOTOR_PIN2 18
#define ENABLE_MOTOR 21

// nfc reader pin
#define SDA_PIN 22
#define SCL_PIN 23

// Adjust the size based on your JSON message, default 256
#define JSON_DIM 256 

// Replace with your Wi-Fi credentials
const char* ssid = "Rete abc";
const char* password = "ciaociaocattai";

// train control
enum speed_level{Slow, Mid_Slow, Moderate, Mid_Fast, Fast};
enum direction{Stop, Forward, Backward};

// websocket
WebSocketsServer webSocket = WebSocketsServer(80);

// nfc class costructor
Adafruit_PN532 nfc(SDA_PIN, SCL_PIN);

// Setting PWM properties
const int freq = 50;
const int pwmChannel = 0;
const int resolution = 8;
int dutyCycle = 200;

// last passed tag
int last_position;


void motor_setUp(){
    pinMode(MOTOR_PIN1, OUTPUT);
    pinMode(MOTOR_PIN2, OUTPUT);
    pinMode(ENABLE_MOTOR, OUTPUT);
    
    // configure LED PWM functionalitites
    ledcSetup(pwmChannel, freq, resolution);
    // attach the channel to the GPIO to be controlled
    ledcAttachPin(ENABLE_MOTOR, pwmChannel);
}

void wifi_setUp(){
    // Connect to Wi-Fi
    WiFi.begin(ssid, password);
    while (WiFi.status() != WL_CONNECTED) {
        delay(1000);
        Serial.println("Connecting to WiFi...");
    }
    Serial.println("Connected to WiFi");
}

void nfc_setUp(){
    nfc.begin();
    uint32_t versiondata = nfc.getFirmwareVersion();
    if (!versiondata) {
        Serial.print("Didn't find PN53x board");
        while (1);
    }
    // configure board to read RFID cards
    nfc.SAMConfig();
    Serial.println("Waiting for an NFC card ...");
}
   
void set_speed(int speed){
    switch (speed){
        case Slow:
            dutyCycle= 50;
            ledcWrite(pwmChannel, dutyCycle);
            break;
        case Mid_Slow:
            dutyCycle= 100;
            ledcWrite(pwmChannel, dutyCycle);
            break;
        case Moderate:
            dutyCycle= 150;
            ledcWrite(pwmChannel, dutyCycle);
            break;
        case Mid_Fast:
            dutyCycle= 200;
            ledcWrite(pwmChannel, dutyCycle);
            break;
        case Fast:
            dutyCycle= 250;
            ledcWrite(pwmChannel, dutyCycle);
            break;
        default:
            Serial.println("default speed");
            dutyCycle= 150;
            ledcWrite(pwmChannel, dutyCycle);
            break;
    }
    
}

void set_direction(direction dir){
    switch (dir){
        case Stop:
            digitalWrite(MOTOR_PIN1, LOW);
            digitalWrite(MOTOR_PIN2, LOW);
            break;
        case Forward:
            digitalWrite(MOTOR_PIN1, HIGH);
            digitalWrite(MOTOR_PIN2, LOW);
            break;
        case Backward:
            digitalWrite(MOTOR_PIN1, LOW);
            digitalWrite(MOTOR_PIN2, HIGH);
            break;
        default:
            Serial.println("default stop");
            digitalWrite(MOTOR_PIN1, LOW);
            digitalWrite(MOTOR_PIN2, LOW);
            break;
    }
}

void send_last_read_position(){
    DynamicJsonDocument doc(JSON_DIM);
    doc["last_read_position"] = String(last_position);
    String message;
    Serial.println("Send message: " + message);
    serializeJson(doc, message);
    webSocket.broadcastTXT(message);
}

void handleWebSocketMessage(String message) {
    Serial.println("Received WebSocket message: " + message);
    
    // Parse JSON message
    DynamicJsonDocument doc(JSON_DIM);
    deserializeJson(doc, message);
    const String action = doc["action"];
    const int value = doc["value"];
    Serial.println("action: " + action+" value: "+value);
    if( action != ""){
        
        // Perform action based on JSON content
        if(action=="stop"){
            set_direction(Stop);
        }
        if(action=="setSpeed"){
            Serial.println("setting speed");
            if(value==0){
                Serial.println("stop");
                set_direction(Stop);
            }else if(value>0){
                Serial.println("forward");
                set_direction(Forward);
                set_speed(value);
            }else{
                Serial.println("backward");
                set_direction(Backward);
                set_speed(value*-1);
            }
            
        }
        if(action=="readPosition"){
            send_last_read_position();
        }
    }
}

void onWebSocketEvent(uint8_t num, WStype_t type, uint8_t * payload, size_t length) {
    switch (type) {
        case WStype_TEXT:
            handleWebSocketMessage(String((char*)payload));
            break;
        case WStype_DISCONNECTED:
            Serial.printf("Disconnected!\n");
            set_speed(Slow);
            set_direction(Stop);
            break;
    }
}

void read_nfc(){
    uint8_t success;
    uint8_t uid[] = { 0, 0, 0, 0, 0, 0, 0 };
    uint8_t uidLength;
    success = nfc.readPassiveTargetID(PN532_MIFARE_ISO14443A, uid, &uidLength);
    if (success) {
        Serial.println("Found an NFC card!");

        Serial.print("UID Length: ");Serial.print(uidLength, DEC);Serial.println(" bytes");
        Serial.print("UID Value: ");
        for (uint8_t i=0; i < uidLength; i++) {
            Serial.print(" 0x");Serial.print(uid[i], HEX);
        }
        Serial.println("");   
    }
}

void setup() {
    
    Serial.begin(115200);

    motor_setUp();
    wifi_setUp();
    last_position=0;
    //nfc_setUp();
    
    // Begin WebSocket server
    webSocket.begin();
    // Set the event handler
    webSocket.onEvent(onWebSocketEvent);

    Serial.println("Train is started");
    
}

void loop() {
    webSocket.loop();
    //read_nfc();
}

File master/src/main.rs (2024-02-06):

use common_infrastructure::{devices::Switch, devices::Train, messages::{SwitchMessage, TrainMessage}, Position};
#[allow(unused_imports)]
use railway_sim_map::SimulatedMap;
#[allow(unused_imports)]
use common_infrastructure::hals::{GenericHal, MasterHal};
use map::views::map_factory::MapFactory;
#[macro_use]
extern crate rouille;
mod low_level_controller;
mod high_level_controller;
mod path_finder_and_scheduler;

mod hal;
use hal::MasterHalRaspberryPi;

type Hal = MasterHalRaspberryPi;
fn main(){
    let r = run();
    if let Err(e) = r{
        println!("Error: {:?}", e);
    }
}


fn run()-> anyhow::Result<()>{
    let hal = Hal::new()?;
    let factory = get_map()?;

    let com = factory.add_comunicator();
    let hlc = high_level_controller::HighLevelController::new(com);

    let mut pfas = path_finder_and_scheduler::PathFinderAndScheduler::new(&hal, &factory);

    loop{
        let request = hlc.get_request()?;
        pfas.add_request(request)?;
        hal.sleep_for_ms(1000);
    }
}

fn get_map()-> anyhow::Result<MapFactory>{

    const DEFAULT_STRAIGHT_SPEED: i8 = 35;
    const DEFAULT_UPHILL_SPEED: i8 = 50;

    let mut map = map::views::MapCreationView::new();

    //// nodes ////
    map.add_nodes(&[
        Position::P1,
        Position::P2,
        Position::P3,
        Position::P4,
        Position::P5,
        Position::P6,
        Position::P7,
        Position::P8,
        Position::P9,
        Position::P10,
        Position::P11,
        Position::P12,
        Position::P13,
        Position::P14,
        Position::P15,
        Position::P16,
        Position::P17,
        Position::P18,
        Position::P19,
        Position::P20,
        Position::P21,
        Position::P22,
        Position::P23,
        Position::P24,
        Position::P25,
        Position::P26
    ])?;
    
    
    map.add_switches(&vec![Switch::S1,Switch::S2,Switch::S3,Switch::S4,Switch::S5,Switch::S6])?;

    //// switch stations ////
    map.add_switch_station(Switch::S1, Position::P21, Position::P2, Position::P5)?;
    map.add_switch_station(Switch::S2, Position::P24, Position::P1, Position::P12)?;
    //map.add_switch_station(Switch::S3, Position::P19, Position::P20, Position::P11)?;
    map.add_switch_station(Switch::S4, Position::P19, Position::P20, Position::P11)?;
    //map.add_switch_station(Switch::S4, Position::P23, Position::P22, Position::P24)?;
    map.add_switch_station(Switch::S5, Position::P6, Position::P16, Position::P7)?;
    map.add_switch_station(Switch::S6, Position::P4, Position::P3, Position::P21)?;


    //// S1 to S4 ////
    map.add_link(Position::P23, Position::P2, 30,DEFAULT_STRAIGHT_SPEED, 50)?;
    
    //// S2 to S3 ////
    map.add_link(Position::P1, Position::P19, DEFAULT_STRAIGHT_SPEED,DEFAULT_STRAIGHT_SPEED, 50)?;

    //// S3 to S5 ////
    map.add_link(Position::P11, Position::P7, 25,DEFAULT_STRAIGHT_SPEED, 50)?;

    //// S5 to S6 ////
    map.add_link(Position::P6, Position::P4, 30,30, 50)?;

    //// S3 to S6 ////
    map.add_link(Position::P3, Position::P17, DEFAULT_STRAIGHT_SPEED,DEFAULT_STRAIGHT_SPEED, 50)?;
    map.add_link(Position::P17, Position::P8, DEFAULT_STRAIGHT_SPEED,DEFAULT_STRAIGHT_SPEED, 50)?;
    map.add_link(Position::P8, Position::P20, DEFAULT_STRAIGHT_SPEED,DEFAULT_STRAIGHT_SPEED, 50)?;

    //// S2 to S5 | bridge ////
    map.add_link(Position::P12, Position::P13, DEFAULT_UPHILL_SPEED,0, 50)?;
    map.add_link(Position::P13, Position::P14, 25,25, 50)?;
    map.add_link(Position::P14, Position::P15, 15,DEFAULT_UPHILL_SPEED, 50)?;
    map.add_link(Position::P15, Position::P16, DEFAULT_STRAIGHT_SPEED,DEFAULT_STRAIGHT_SPEED, 50)?;

    //// dead track S1 ////
    map.add_link(Position::P5, Position::P25, DEFAULT_STRAIGHT_SPEED,DEFAULT_STRAIGHT_SPEED, 50)?;
    map.add_link(Position::P25, Position::P18, DEFAULT_STRAIGHT_SPEED,DEFAULT_STRAIGHT_SPEED, 50)?;
    

    //// trains ////
    map.add_train(Train::T2, Position::P23, Some(Position::P2))?;
    map.add_train(Train::T1, Position::P18, None)?;
    
    
    //// creation ////
    let factory: MapFactory = map.into();
    Ok(factory)
}


#[test]
fn test_all_connections(){
    let hal = Hal::new().unwrap();

    for train in [Train::T1,Train::T2]{
        println!("Testing {:?} connection...",train);
        let _ = hal.send_message_to_train(train, TrainMessage::SetSpeed(0)).map_err(|e|{
            eprintln!("{:?} is not connected: {}",train,e);
        });
    }

    for switch in [Switch::S1,Switch::S2,Switch::S3,Switch::S4,Switch::S5,Switch::S6]{
        println!("Testing {:?} connection...",switch);
        let _ = hal.send_message_to_switch(switch, SwitchMessage::SetPositionDiverted).map_err(|e|{
            eprintln!("{:?} is not connected: {}",switch,e);
        });
    }
}

#[test]
fn receiver_test(){
    let hal = Hal::new().unwrap();
    loop {
        while let Some(m) = hal.get_message().unwrap() {
            println!("Got message: {m:?}")
        }
    }
}

#[test]
fn test_send_message(){
    let hal = Hal::new().unwrap();
    hal.send_message_to_switch(Switch::S1, SwitchMessage::SetPositionStraight).unwrap();
    return;
    loop {
        hal.send_message_to_train(common_infrastructure::devices::Train::T2, common_infrastructure::messages::TrainMessage::SetSpeed(0)).unwrap();
        hal.sleep_for_ms(2000);
        return;
        hal.send_message_to_train(common_infrastructure::devices::Train::T1, common_infrastructure::messages::TrainMessage::SetSpeed(80)).unwrap();
        hal.sleep_for_ms(2000);
        hal.send_message_to_train(common_infrastructure::devices::Train::T1, common_infrastructure::messages::TrainMessage::SetSpeed(100)).unwrap();
        hal.sleep_for_ms(2000);
    }
}

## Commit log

2023-10-02 Update README.md
    change name to rusty railways
2023-11-11 add examples
    [partition_table.csv]
2023-12-14 add initialization of switch_controller
2023-12-20 modified: src/main.cpp
    now sg90 motor works
2023-12-22 add switch station tests
2023-12-22 add train insertion tests
2023-12-29 add find path to switch point
2023-12-29 add debug print to low level controller
2024-01-16 add and create train program new file: test/.gitignore new file: test/move/.gitignore new file: test/move/Cargo.toml new file: test/move/build.rs new file: test/move/makefile new file: test/move/part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
    [partition_table.csv]
2024-01-17 Add template
    [partition_table.csv]
2024-01-18 locomotive rust version modified: test/move/Cargo.toml modified: test/move/src/main.rs deleted: train/Cargo.toml renamed: train/.cargo/config.toml -> train/rust/.cargo/config.toml renamed: train/.git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
    [partition_table.csv]
2024-01-18 add cpp part, useful for testing new file: train/cpp/.gitignore new file: train/cpp/arduinoWebSockets new file: train/cpp/include/README new file: train/cpp/lib/README new file: train/cpp/platformio.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
2024-01-18 add switch and train control test
    new file: quick_tests/control_test/test.py
    modified: .gitignore
    modified: train/cpp/arduinoWebSockets (modified content)
2024-01-20 add nfc driver
2024-01-20 finish fixing compile error of train hal
    [main.rs]
2024-01-22 Switch part
    new file: switch/include/README
    new file: switch/lib/README
    new file: switch/platformio.ini
    new file: switch/readme.txt
    new file: switch/src/.main.old.cpp
    new file: switch/src/main.cpp
    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
2024-01-25 add the possibility to update via OTA modified: switch/platformio.ini deleted: switch/src/.main.old.cpp modified: switch/src/main.cpp deleted: esp8266/include/README deleted: esp8266/lib/README delet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
2024-01-31 modified: switch/angles.txt
2024-01-31 bug fixing 1 modified: src/main.cpp
    [main.cpp]
2024-01-31 bug fixed, host name modified: platformio.ini modified: src/main.cpp
    [main.cpp]
2024-01-31 Remove OTA because it cause some critial errors modified: switch/platformio.ini modified: switch/src/main.cpp
    [main.cpp]
2024-01-31 modified: switch/platformio.ini
2024-01-31 Add better switching low level controller
2024-01-31 Add switch 3
2024-01-31 Add Rusty Railways logo
2024-01-31 Add client/train-track-pieces directory and some placeholder low quality images for now
2024-01-31 Update client/train-track-pieces placeholders with custom-made vector images for the track pieces, thanks to tuttograficamarta.it for the help!
2024-01-31 Add image to remember what parameters to use when generating CollisionPolygon2Ds for the train track pieces
2024-01-31 Add BaseTrainTrackPiece (base reference Node for all train track pieces)
2024-01-31 Add Godot .import files for all client/train-track-piece images
2024-01-31 Add Switch and SwitchFlippedVertically nodes in client/train-track-pieces
2024-01-31 Add SwitchHalfCurve and SwitchHalfCurveFlippedVertically nodes in client/train-track-pieces
2024-01-31 Add QuarterStraight node in client/train-track-pieces
2024-01-31 Add HalfStraight node in client/train-track-pieces
2024-01-31 Add LongStraight node in client/train-track-pieces
2024-01-31 Add LongCurve and LongCurveFlippedVertically nodes in client/train-track-pieces
2024-01-31 Add HalfCurve and HalfCurveFlippedVertically nodes in client/train-track-pieces
2024-01-31 Add Curve and CurveFlippedVertically nodes in client/train-track-pieces
2024-01-31 Add ConnectionPoint.gd script (for all ConnectionPoints in all train track pieces)
2024-01-31 Add Rusty Railways client logo and relative Godot .import file
2024-01-31 Add coi_serviceworker Godot plugin to bypass js SharedArrayBuffer header requirements (https://developer.mozilla.org/en-US/docs/Web/JavaScript/Reference/Global_Objects/SharedArrayBuffer) when buildin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
    [plugin.cfg]
2024-01-31 Add client/export_presets.cfg (Godot project export/build presets)
    [export_presets.cfg]
2024-01-31 Fix broken dependency in client/train-track-pieces/BaseTrainTrackPiece.tscn
2024-02-01 Change train track spawner locations in client/Main.tscn (they are organized now)
2024-02-01 Add default train track in client/Main.tscn (it's the track we currently have set up physically)
2024-02-01 Add force update connections functionality to client
    now you can build train track in the Godot editor itself, and they will correctly connect together when you run the client!
2024-02-01 Change some Camera settings in client/Main.tscn
2024-02-01 Change arrows of client switches to headless arrows
    this is done because it better represents the fact that the switch is both ways
2024-02-01 add code documentations, readme, 3d and pcb files
    new file: doc/cpp_part/html/bc_s.png
    new file: doc/cpp_part/html/bdwn.png
    new file: doc/cpp_part/html/closed.png
    new file: doc/cpp_part/html/doc.png
    new file: doc/cpp_part/html/doxygen.css
    new file: doc/cpp_part/html/doxygen.svg
    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
    [Asse.stl, P1.stl, P2.stl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]
2024-02-01 Switch and Train documentation
2024-02-02 Add setting switch a tag before arriving to the switch corresponding tag.
2024-02-07 Add of PCB and Board images
2024-02-07 Add KiCAD PCB image
2024-02-07 Add switch board schematic
2024-02-07 Add schematics description
2024-02-07 Fix switch readme.md
2024-02-07 Remove test folder because it's not useful anymore
    [partition_table.csv]
2024-02-07 Tidy up Switch hardware directories
    [Switch_PCB_ESP01.kicad_pcb, Switch_PCB_ESP01.kicad_sch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]
2024-06-18 Update client/README.md with currently broken warning
